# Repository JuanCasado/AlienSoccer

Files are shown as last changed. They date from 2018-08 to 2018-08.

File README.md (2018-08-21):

# AlienSoccer

This project was made by a team of three students that I was part of at Complubot.

We built two robots that played soccer coordinately with a ball that emited infrared light.
The robots were able to detect the ball as well as recognize certain parts of the field like the white limitational lines on it that the robots couldn't cross. Also they detected the field's walls as well as each other using ultrasounds.
Both robots where identically built and the operated with the same software, anyway we had different game modes like goalkeeper or player to modify their behavior.

[View in prezi (Spanish)](https://prezi.com/view/UruUJdG32kYzkdQXmuUq "prezi")

## Main caracteristics
* **High modularity:** the robots had eight processors distributed along them, each one was in charge of a specific task, making every part of the robot independent of the others. We detected wich parts where connected to the robot and operate eith them. Also one independant part could make all its functionality without the others. This made much easier the building procces because we could work in multiple parts of the robot at the same time, also testing them was faster. If one part was damaged during a game we could replace it completely with a new one in less than a minute, also the same part could operate in any robot.
* **Friendly interface:** the robots had a set of buttons, a cirular array of leds and a speaker so at any moment we could be displaying whatever the robots were seeing by their sensors. Having a nice interface was critical mainly because it made testing much easier and faster.
* **Fast processing:** We had had eight Arduino processors distributed along each robot so we where doing hadrware parallelism at any time, the robots could reach a max cycle of sensor refresing of 50ms including processing the information, and decision making.

## Parts of the robots
* **Compass:** The robots could know where they were facing to target the enemy goal.
* **Ultrasounds:** The robots could measure distances of the walls and detect objects.
* **Ball sensor:** Each robot had a "donut" of sensor arroun it, the function of this "donut" was to determine the possition and distance of the ball.
* **UI:** thanks to a set of buttons, a speaker and a circular array of leds we could "talk" to the robot.
* **Floor sensors:** We had four arrays of six sensors each that could read the wite lines of the field.
* **Motors:** Along with the ball sensors this was one of the critical parts of the robot. The robots had for motor each disposed in an X form to make an omnidirectional platform. Each motor was ruled by one proccesor wich made PID control to the motor, the four motor processors were ruled by another one wich made PID control with the facing possition and the ball position and distance to decide the target velocities of the motors, the processors comunicated by i2c.
* **Main board:** we had an arduino Mega as master of all the other seven processors, here the robots made the most critical decissions.

[Mr.BlissfulGrin](http://www.mrblissfulgrin.com "mrblissfulgrin")

[Complubot](http://complubot.com/inicio/ "complubot")

## Promotional video
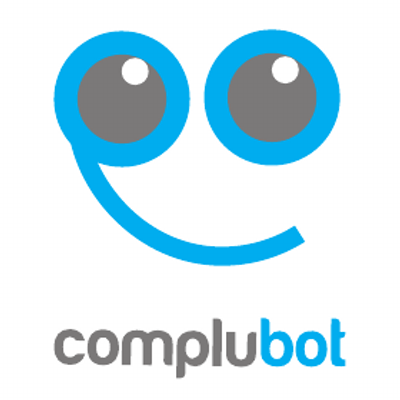
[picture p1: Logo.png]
Imperdibles2.0 Complubot
Imperdibles2.0 (http://www.youtube.com/watch?v=aCtYLtXQVko) 
**Share the video with:** [https://youtu.be/aCtYLtXQVko](https://youtu.be/aCtYLtXQVko "https://youtu.be/aCtYLtXQVko")

## Fist tests
FistTest (https://youtu.be/rDMKiselTD4)

**Share the video with:** [https://youtu.be/rDMKiselTD4](https://youtu.be/rDMKiselTD4 "https://youtu.be/rDMKiselTD4")

## Images
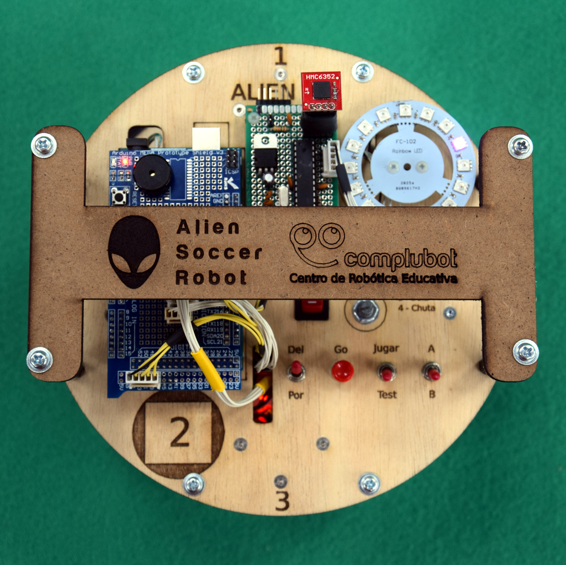
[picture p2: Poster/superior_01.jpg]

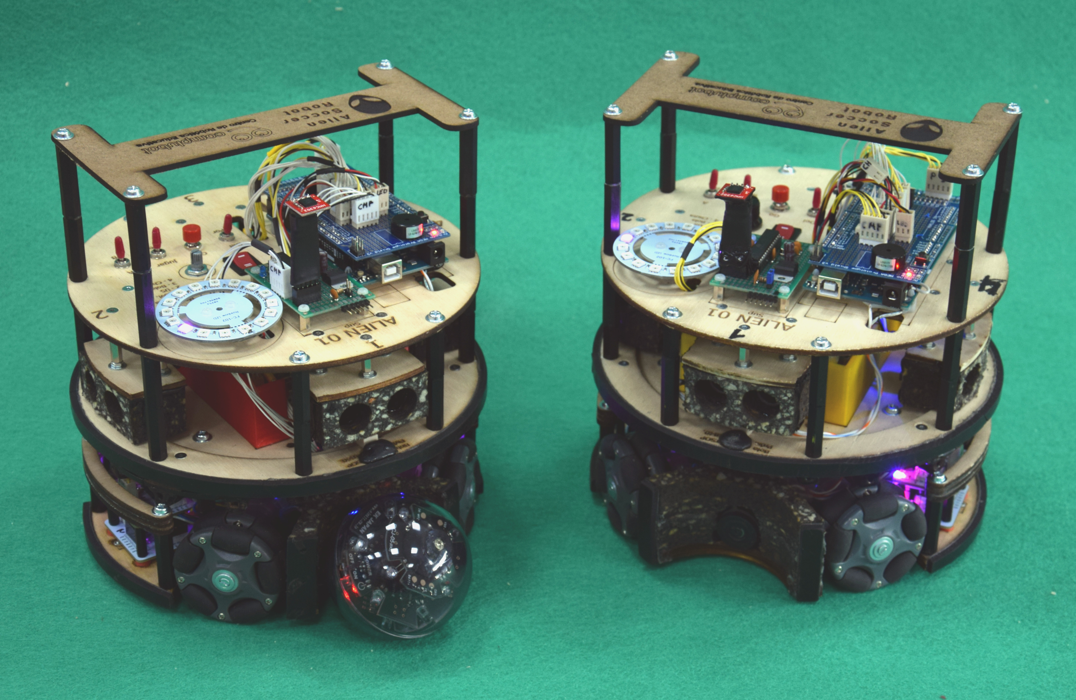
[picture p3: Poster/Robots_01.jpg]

Complubot
Complubot
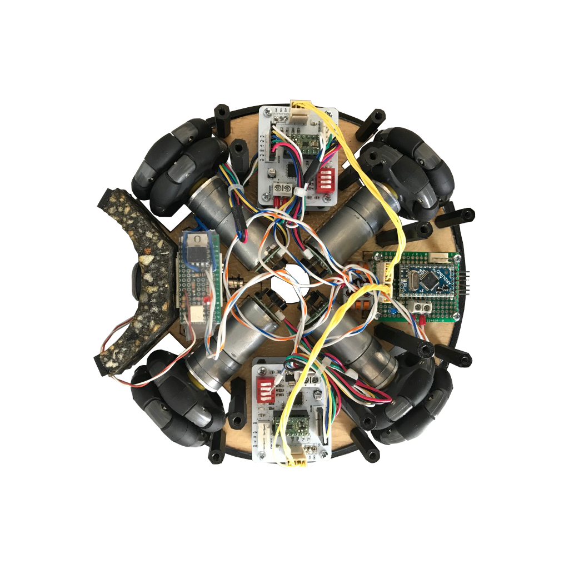
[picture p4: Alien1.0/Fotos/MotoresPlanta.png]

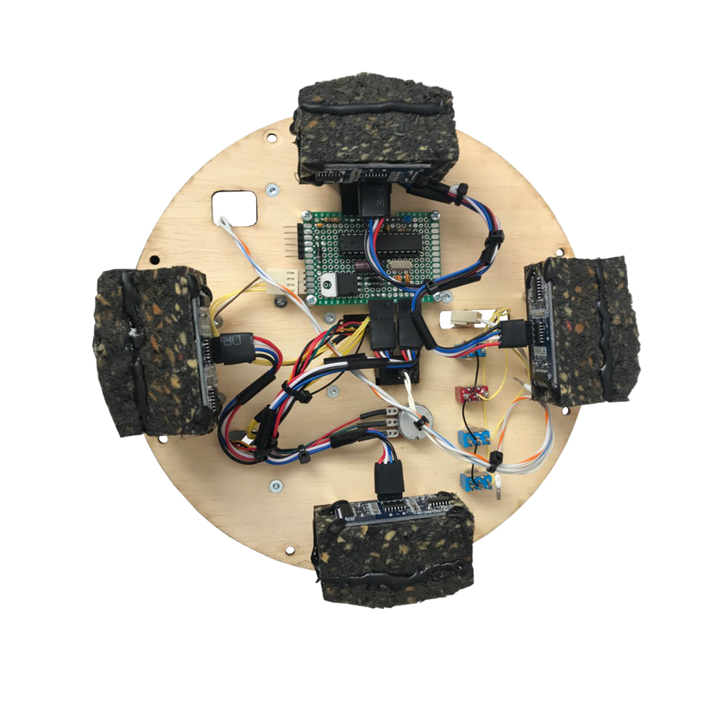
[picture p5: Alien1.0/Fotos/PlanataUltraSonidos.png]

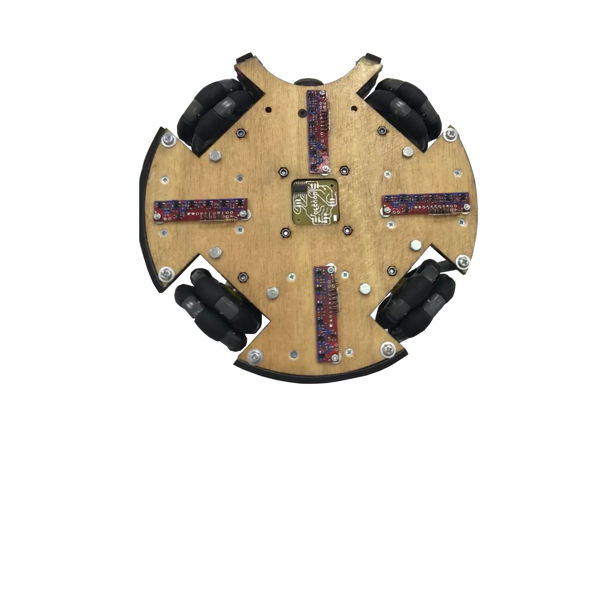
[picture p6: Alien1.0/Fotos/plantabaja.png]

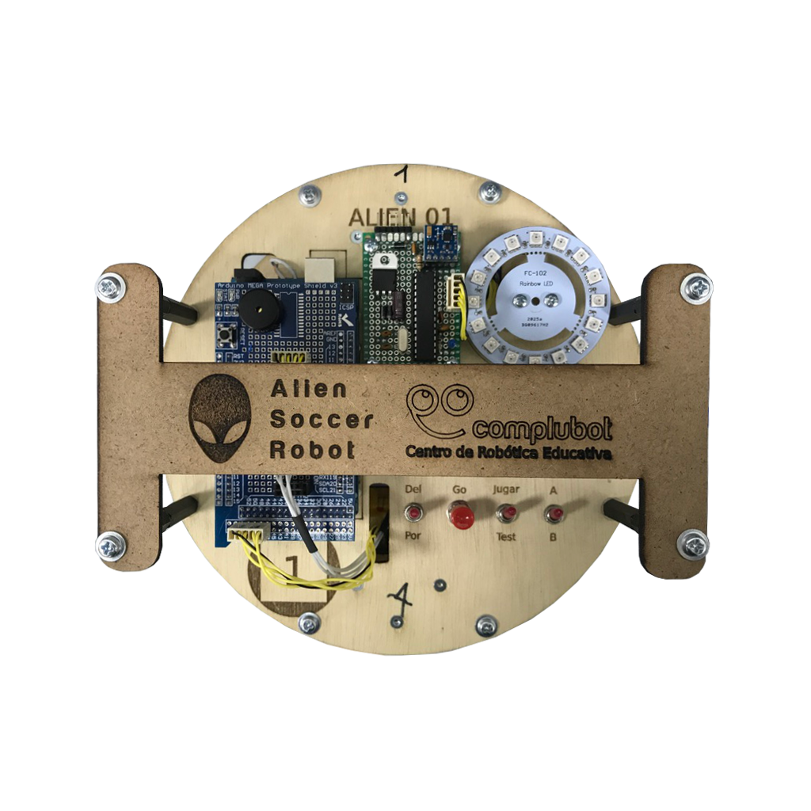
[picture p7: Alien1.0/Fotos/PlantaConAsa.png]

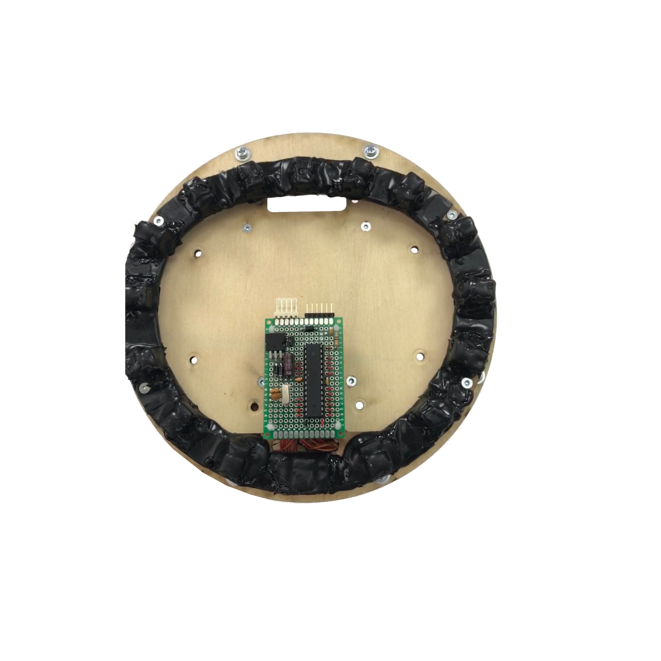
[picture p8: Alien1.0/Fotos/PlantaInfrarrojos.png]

Complubot
Complubot
Complubot
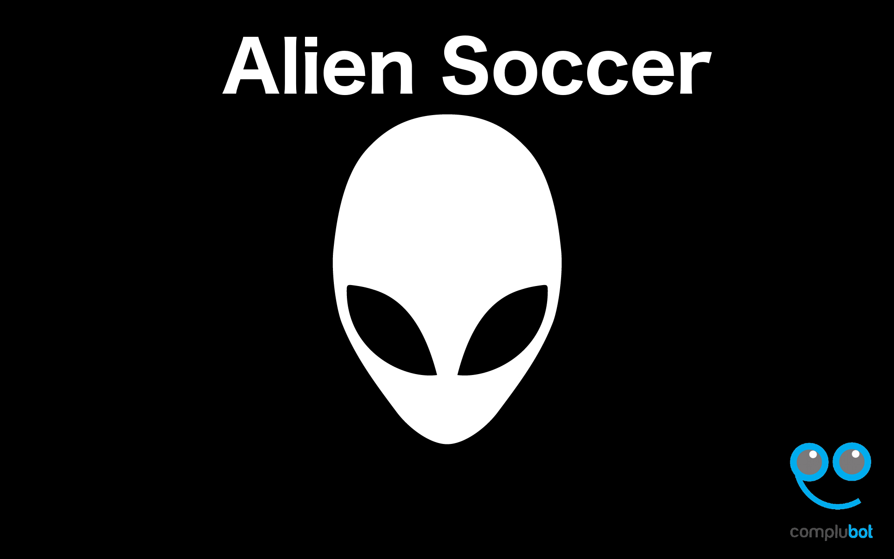
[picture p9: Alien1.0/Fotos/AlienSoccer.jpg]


Project done by Juan Casado Ballesteros

[Mr.BlissfulGrin](http://www.mrblissfulgrin.com "mrblissfulgrin")

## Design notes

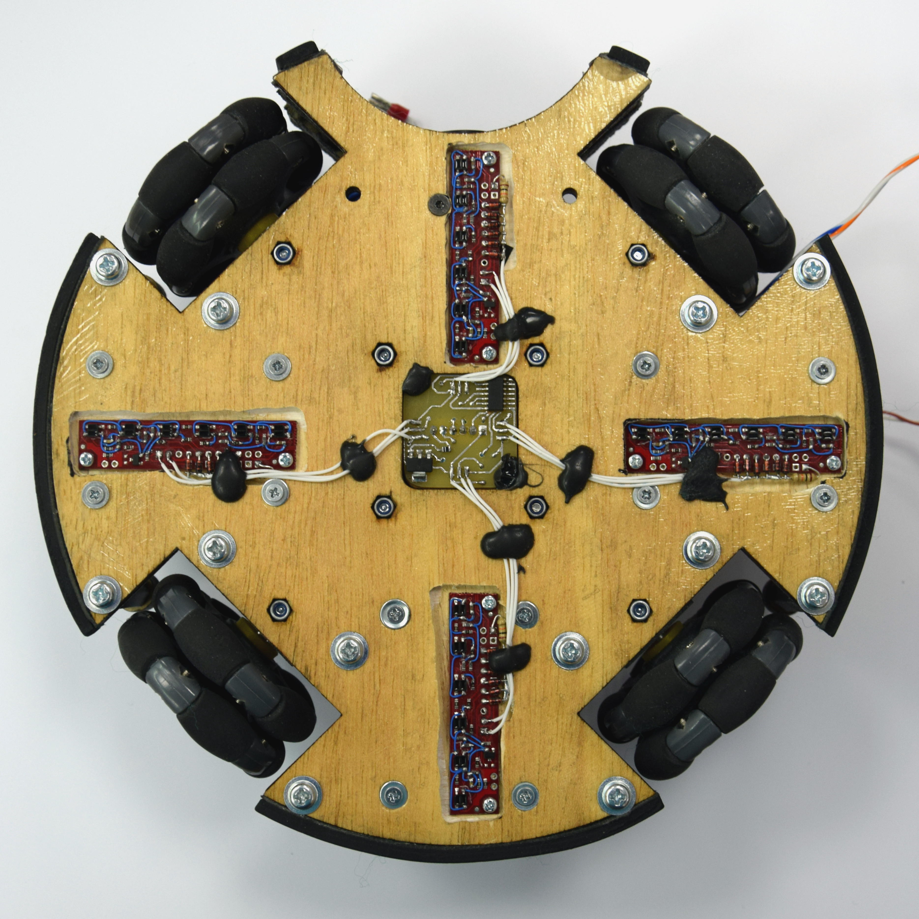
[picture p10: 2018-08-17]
Alien1.0/Poster/inferior.jpg

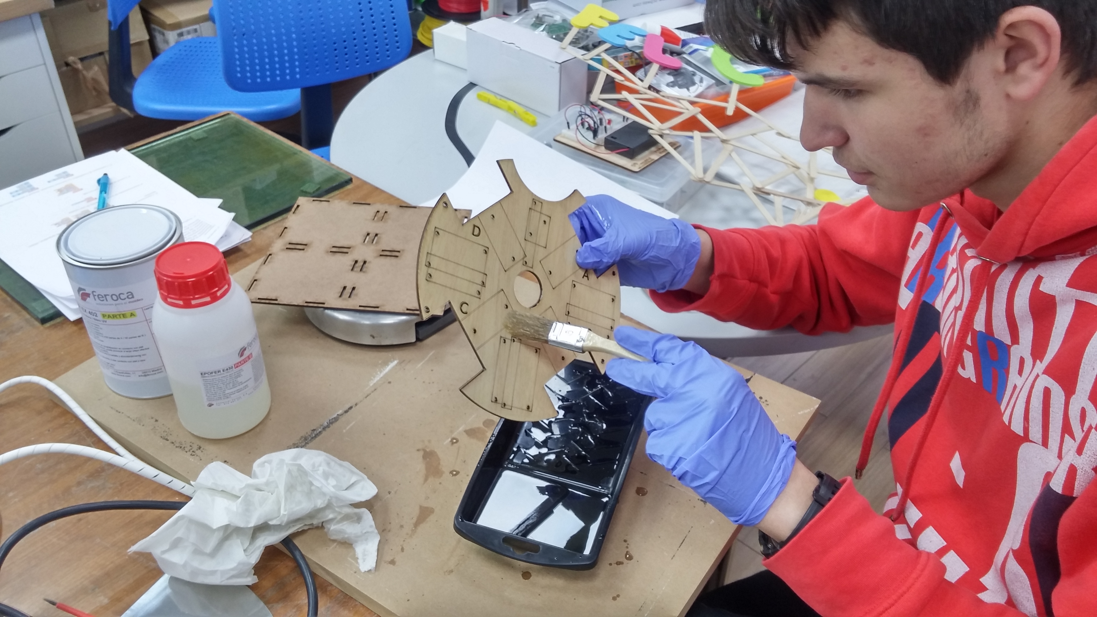
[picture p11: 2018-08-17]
Alien1.0/Poster/20170323_155203_HDR.jpg

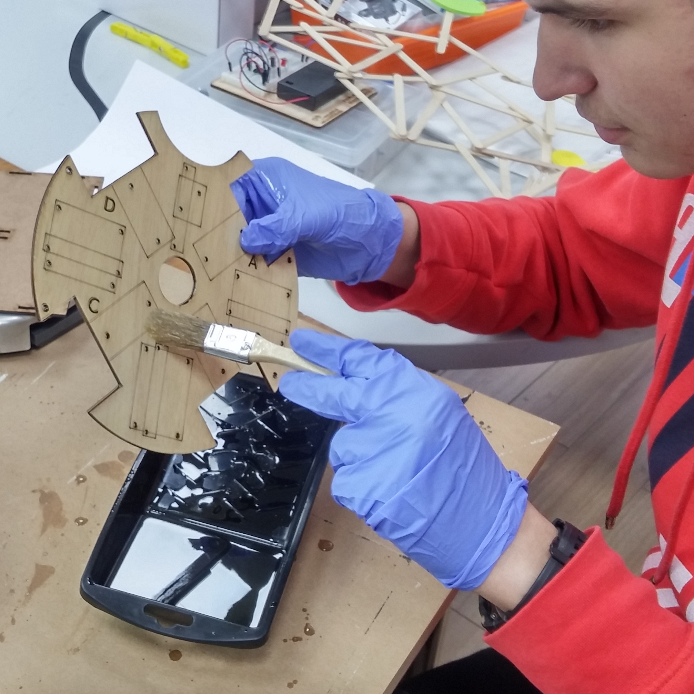
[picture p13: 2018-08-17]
Alien1.0/Poster/resina_01.jpg

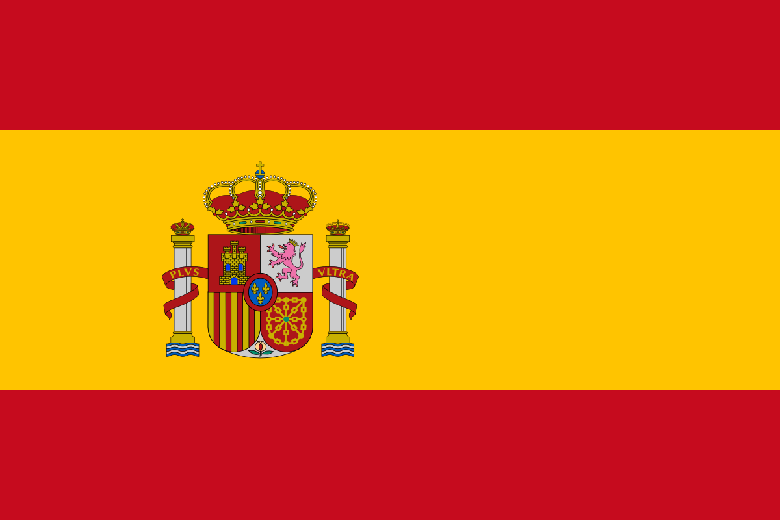
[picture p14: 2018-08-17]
Alien1.0/Poster/Flag_of_Spain.png

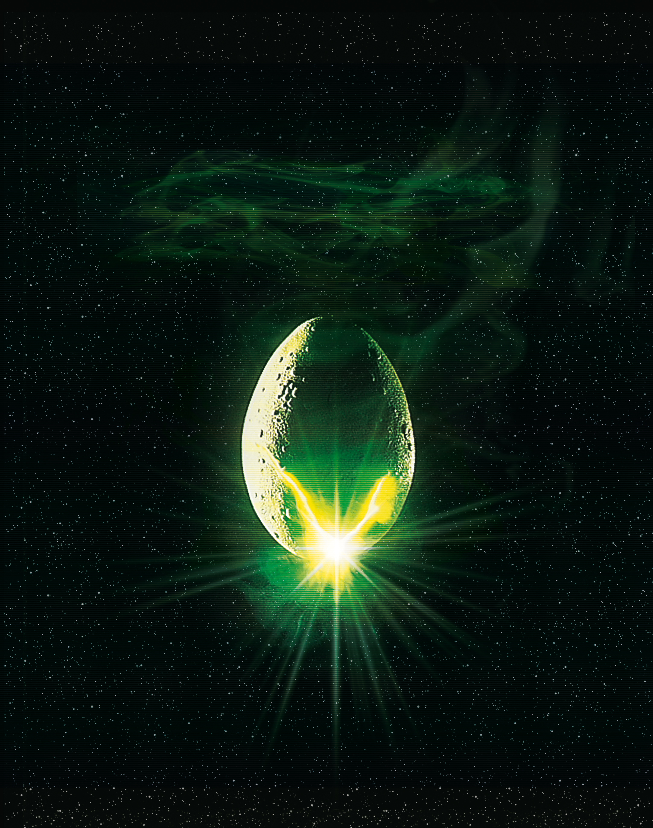
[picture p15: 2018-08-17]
Alien1.0/Poster/cc1d4e6140e174dd6c340d02d83366ad.jpeg

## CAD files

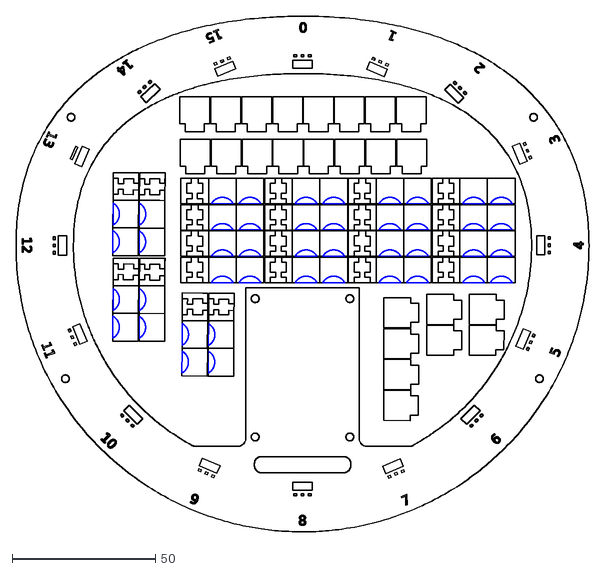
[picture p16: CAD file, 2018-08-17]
Alien1.0/Alien_Corte_Laser/Alien_ball_04.dxf
199.7 x 179.7

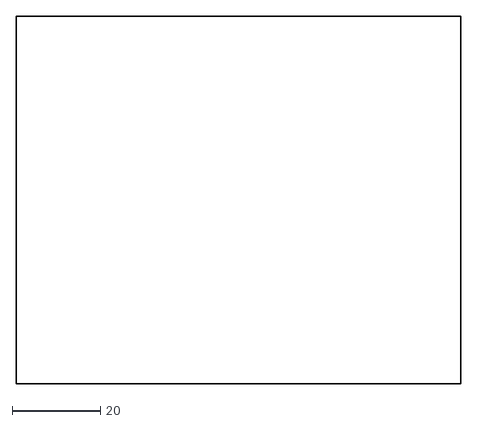
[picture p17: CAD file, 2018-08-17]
Alien1.0/KiCad/Alien_Power/pcb_shape.dxf
101.0 x 83.4

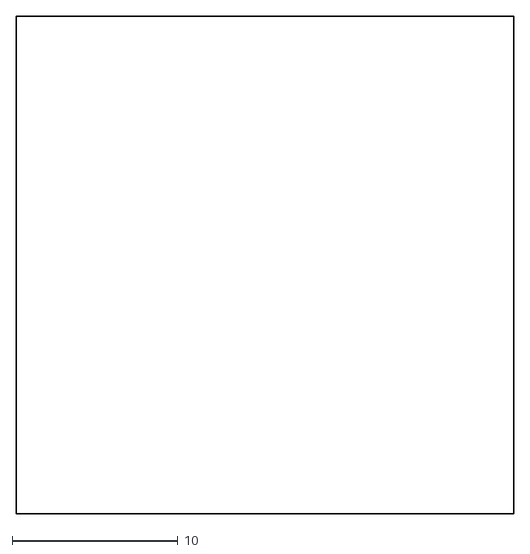
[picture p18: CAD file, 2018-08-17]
Alien1.0/KiCad/Alien_S_Suelo/pcb_shape.dxf
30.0 x 30.0

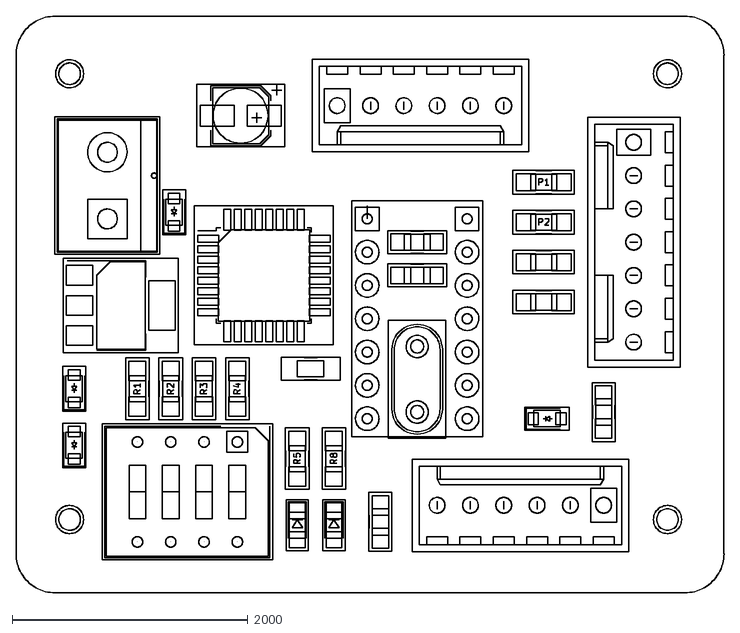
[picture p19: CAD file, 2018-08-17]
Alien1.0/KiCad/Driver_alien/Driver_alien-brd.dxf
6000.2 x 4889.2

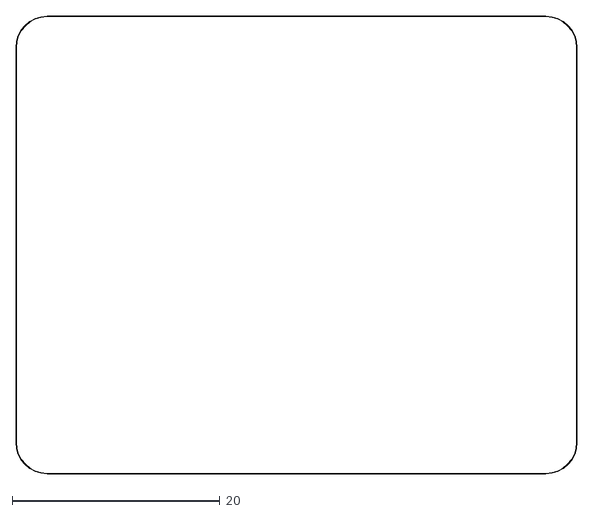
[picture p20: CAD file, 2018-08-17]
Alien1.0/KiCad/pcb_shape.dxf
54.0 x 44.0

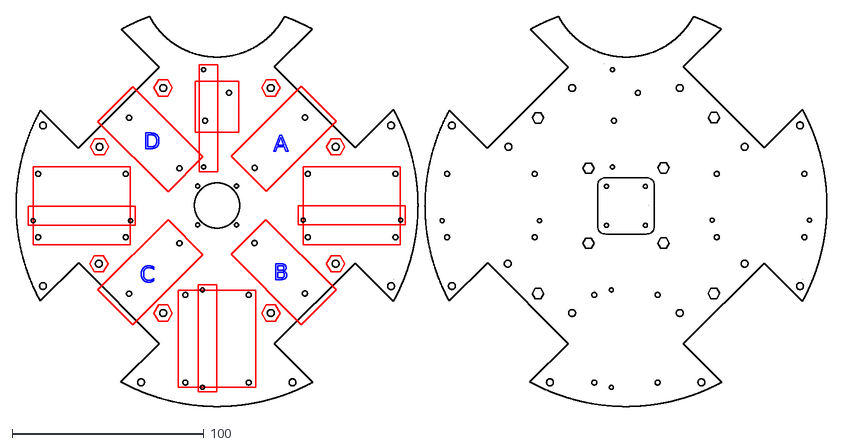
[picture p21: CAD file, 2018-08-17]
Alien1.0/Alien_Corte_Laser/Alien_motor_base_final.dxf
423.1 x 203.5

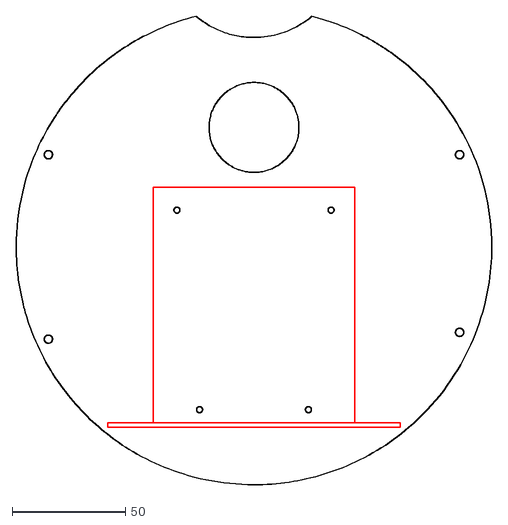
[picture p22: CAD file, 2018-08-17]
Alien1.0/Alien_Corte_Laser/Alien_Intermedio_Base_01.dxf
209.7 x 206.6

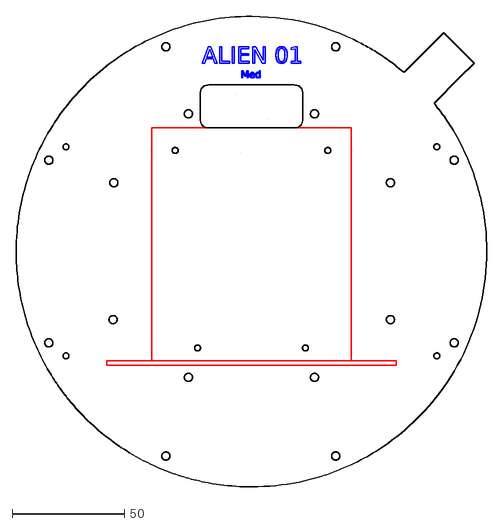
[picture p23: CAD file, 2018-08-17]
Alien1.0/Alien_Corte_Laser/Alien_Intermedio_Base_02_recorte.dxf
209.6 x 209.6

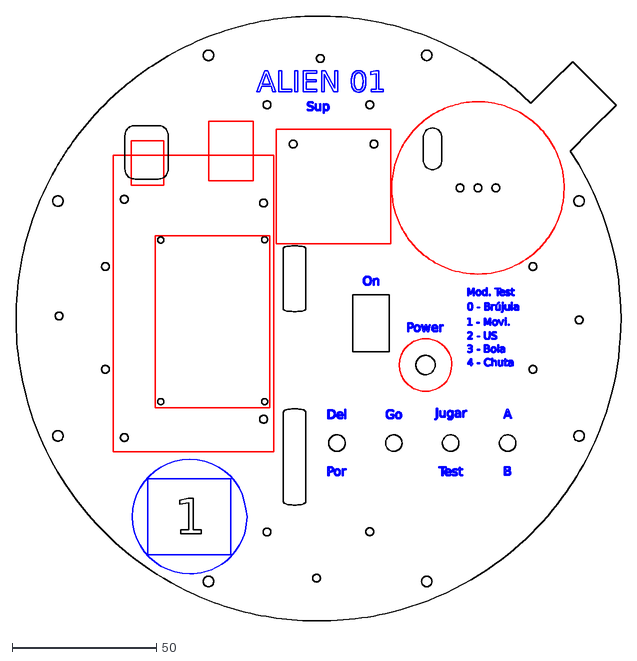
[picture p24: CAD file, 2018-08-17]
Alien1.0/Alien_Corte_Laser/Alien_Master_Base_03_recorte.dxf
209.6 x 209.6

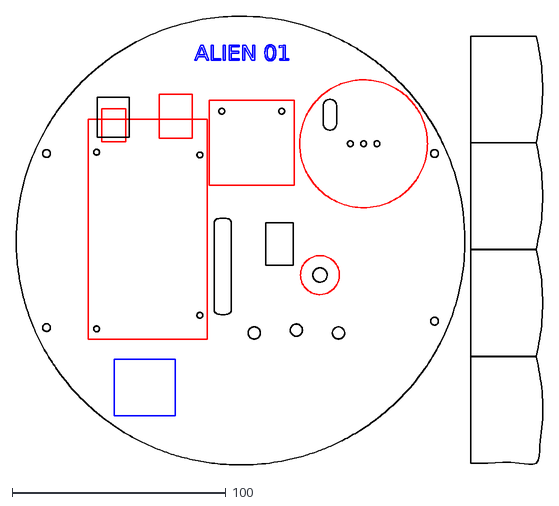
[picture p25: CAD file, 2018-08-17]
Alien1.0/Alien_Corte_Laser/Alien_Master_Base_01.dxf
246.1 x 210.1

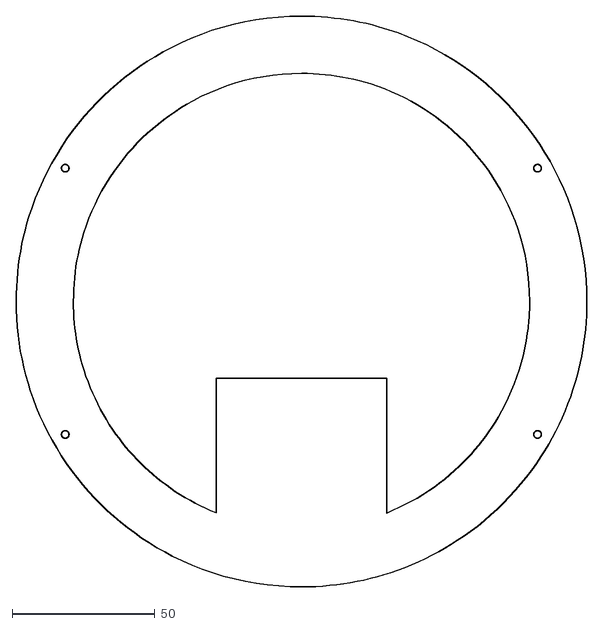
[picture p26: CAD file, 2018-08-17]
Alien1.0/Alien_Corte_Laser/Alien_ball_01.dxf
199.6 x 199.6

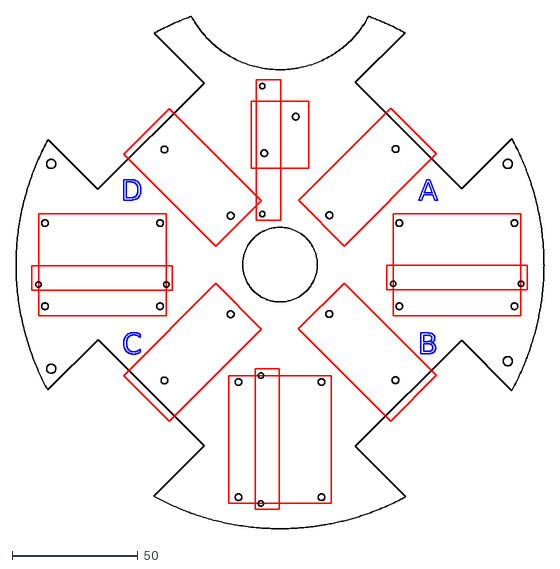
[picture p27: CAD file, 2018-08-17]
Alien1.0/Alien_Corte_Laser/Alien_motor_base_01.dxf
209.7 x 203.5

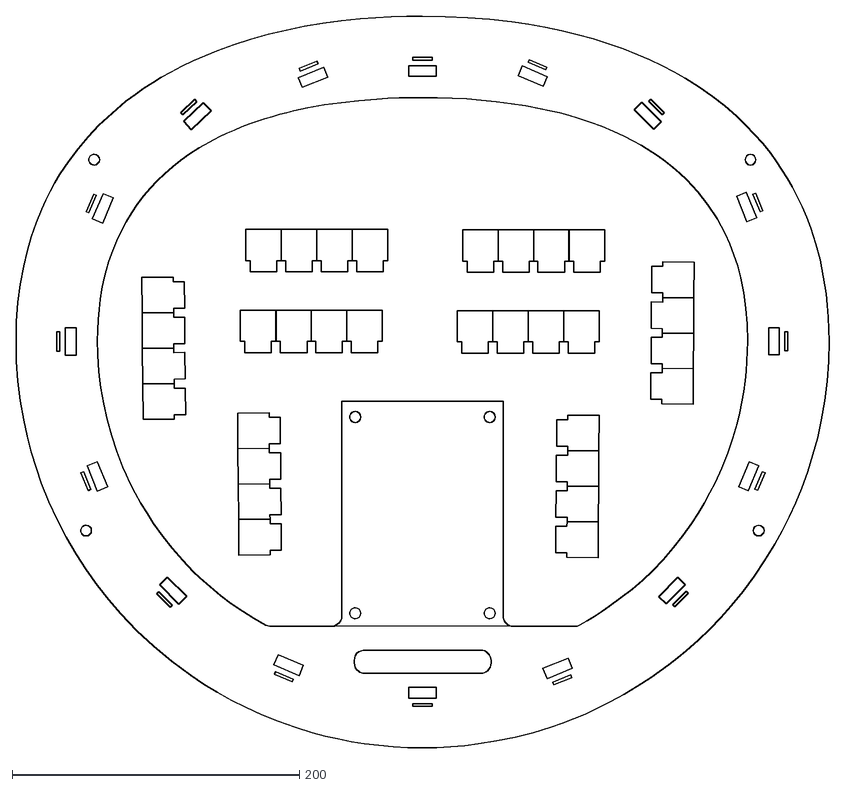
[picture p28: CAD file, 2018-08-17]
Alien1.0/Alien_Corte_Laser/Alien_ball_02.dxf
566.1 x 509.4

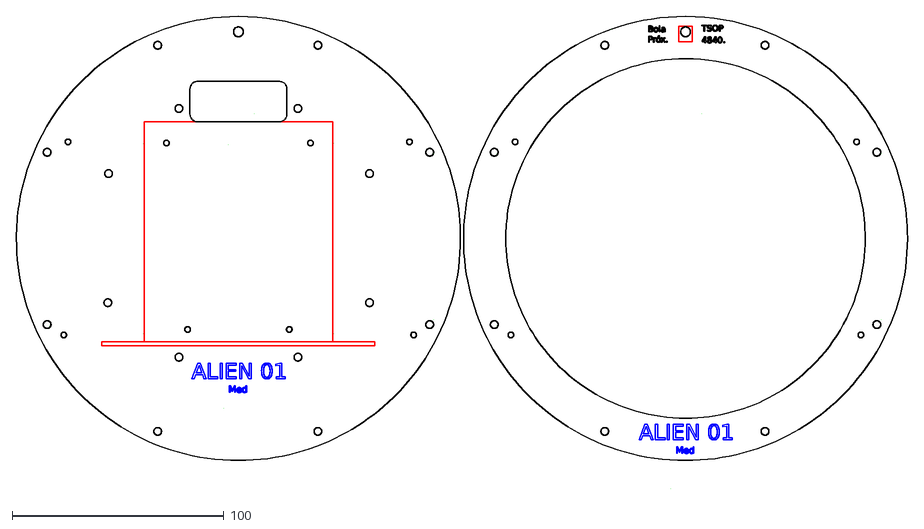
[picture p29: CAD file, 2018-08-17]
Alien1.0/Alien_Corte_Laser/Alien_Intermedio_Base_04.dxf
420.7 x 222.9

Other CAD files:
Alien1.0/Alien_Corte_Laser/Alien_Master_Base_03-2.dxf
Alien1.0/Alien_Corte_Laser/Alien_motor_base_03_contra.dxf
Alien1.0/Alien_Corte_Laser/Asa_01.dxf
Alien1.0/Alien_Corte_Laser/Alien_ball_01-2.dxf
Alien1.0/Alien_Corte_Laser/Alien_Chutador_01.dxf
Alien1.0/Alien_Corte_Laser/Alien_Intermedio_Base_02.dxf
Alien1.0/Alien_Corte_Laser/Alien_Intermedio_Base_03.dxf
Alien1.0/Alien_Corte_Laser/Alien_Master_Base_02-2.dxf
Alien1.0/Alien_Corte_Laser/Alien_Master_Base_02.dxf
Alien1.0/Alien_Corte_Laser/Alien_Master_Base_03.dxf
Alien1.0/Alien_Corte_Laser/Alien_motor_base_02.dxf
Alien1.0/Alien_Corte_Laser/Alien_motor_base_03.dxf
Alien1.0/Alien_Corte_Laser/Driver_alien-brd.dxf
Alien1.0/Alien_Corte_Laser/espumas_us_01.dxf
Alien1.0/Alien_Corte_Laser/espumas_us_02.dxf

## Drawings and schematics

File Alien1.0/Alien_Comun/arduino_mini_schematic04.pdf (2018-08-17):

# ARDUINO MINI 04

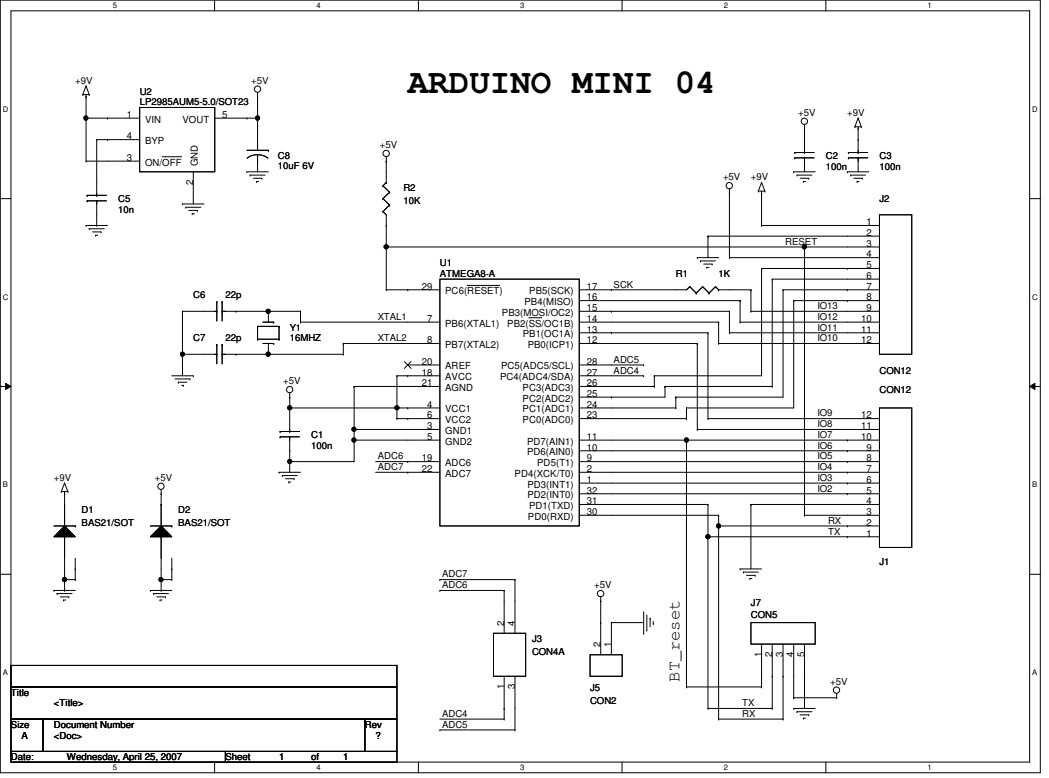
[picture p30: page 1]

PB0(ICP1) 12 PB1(OC1A) 13 PB2(SS/OC1B) 14 PB3(MOSI/OC2) 15 PB4(MISO) 16 PB5(SCK) 17

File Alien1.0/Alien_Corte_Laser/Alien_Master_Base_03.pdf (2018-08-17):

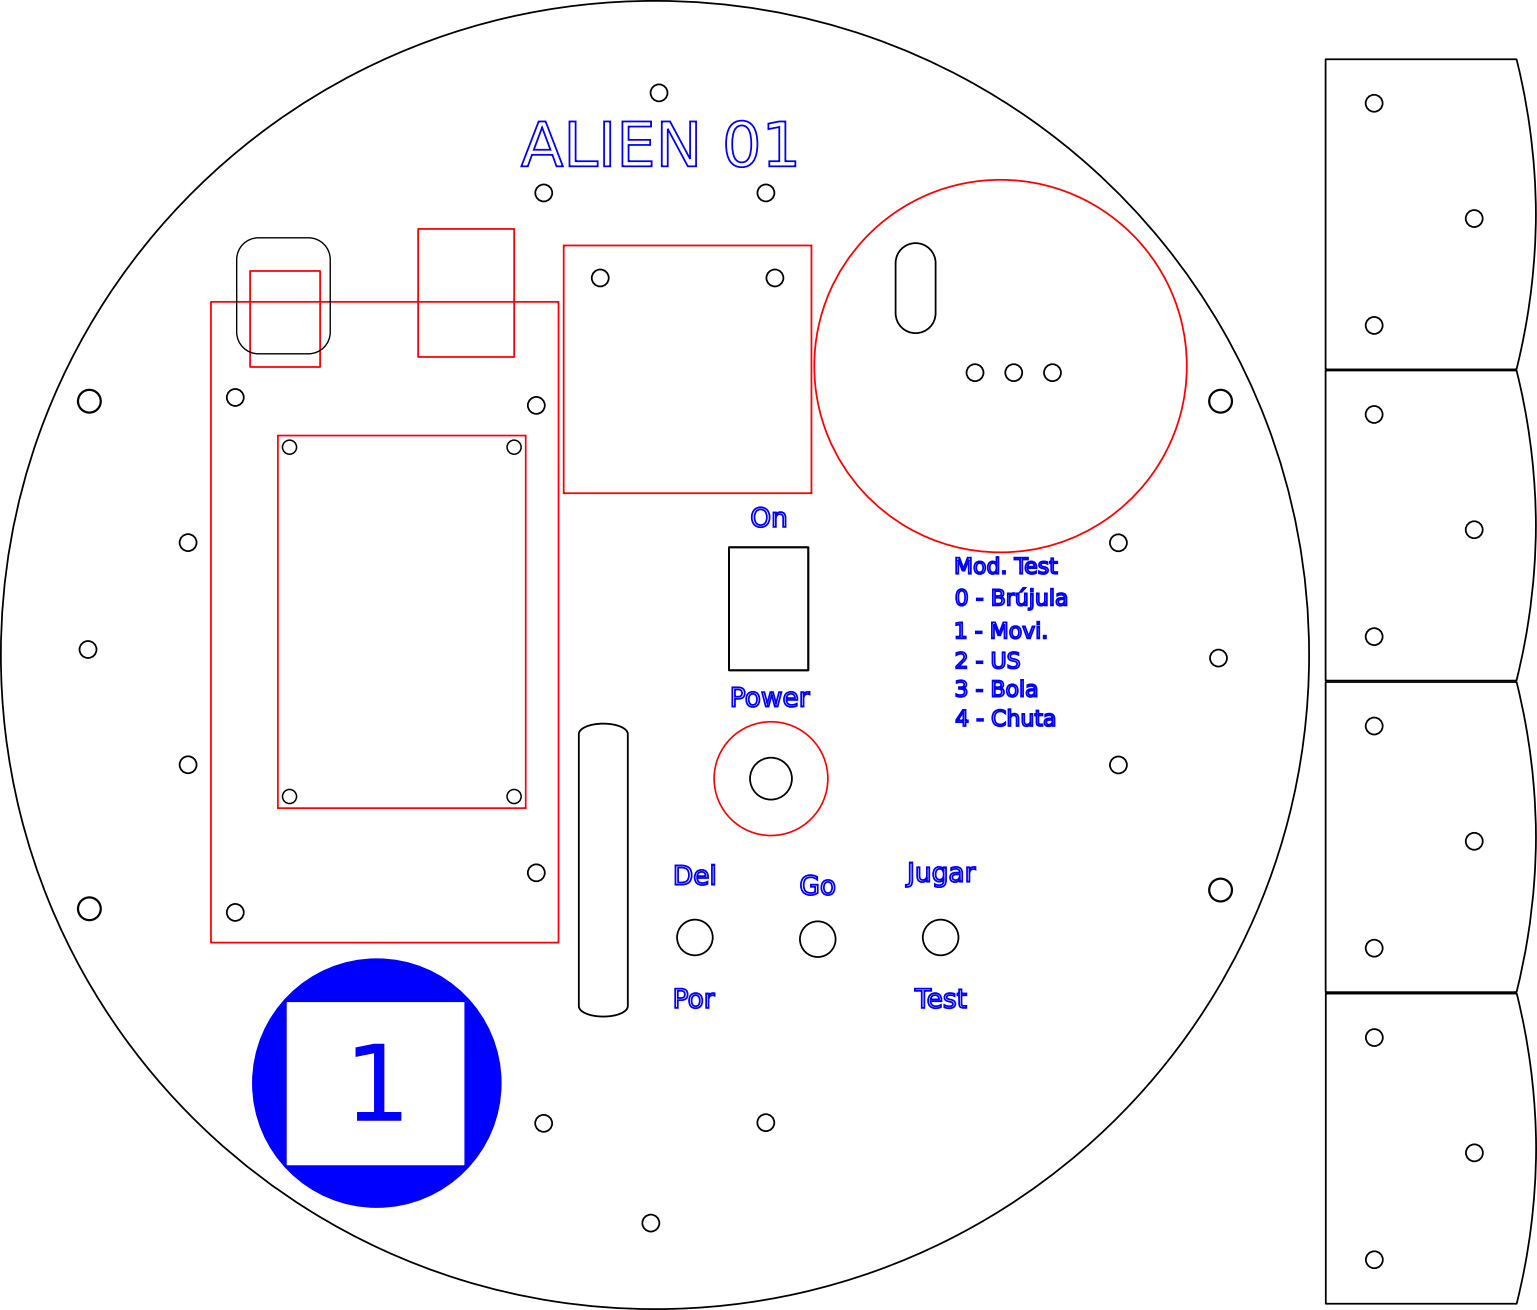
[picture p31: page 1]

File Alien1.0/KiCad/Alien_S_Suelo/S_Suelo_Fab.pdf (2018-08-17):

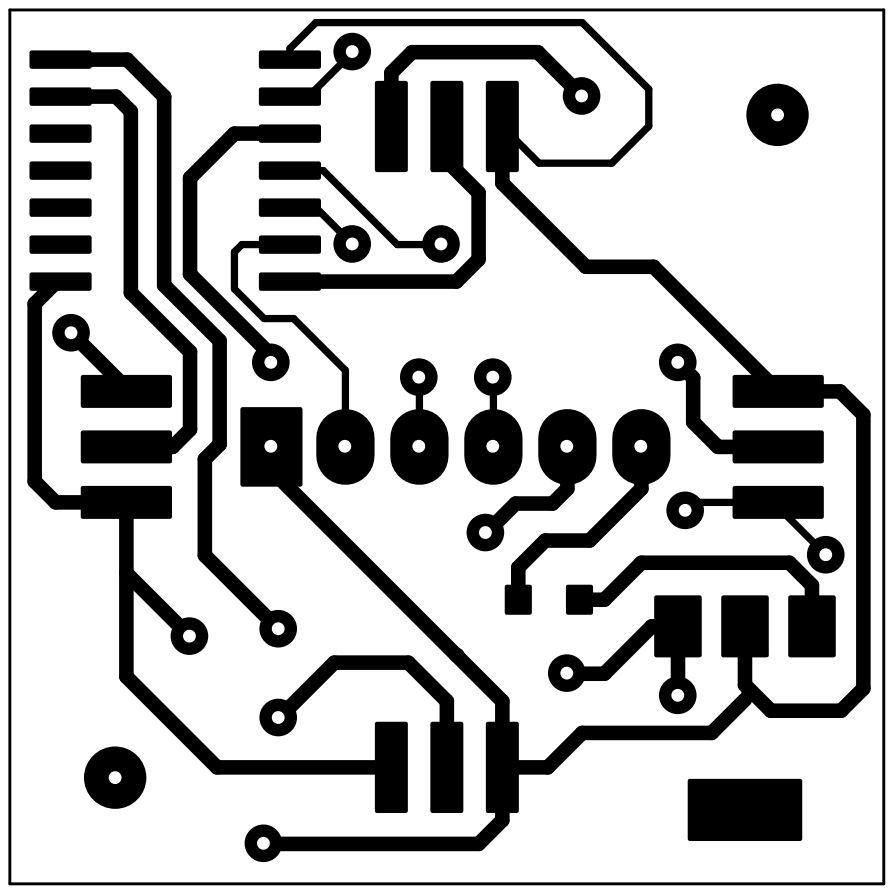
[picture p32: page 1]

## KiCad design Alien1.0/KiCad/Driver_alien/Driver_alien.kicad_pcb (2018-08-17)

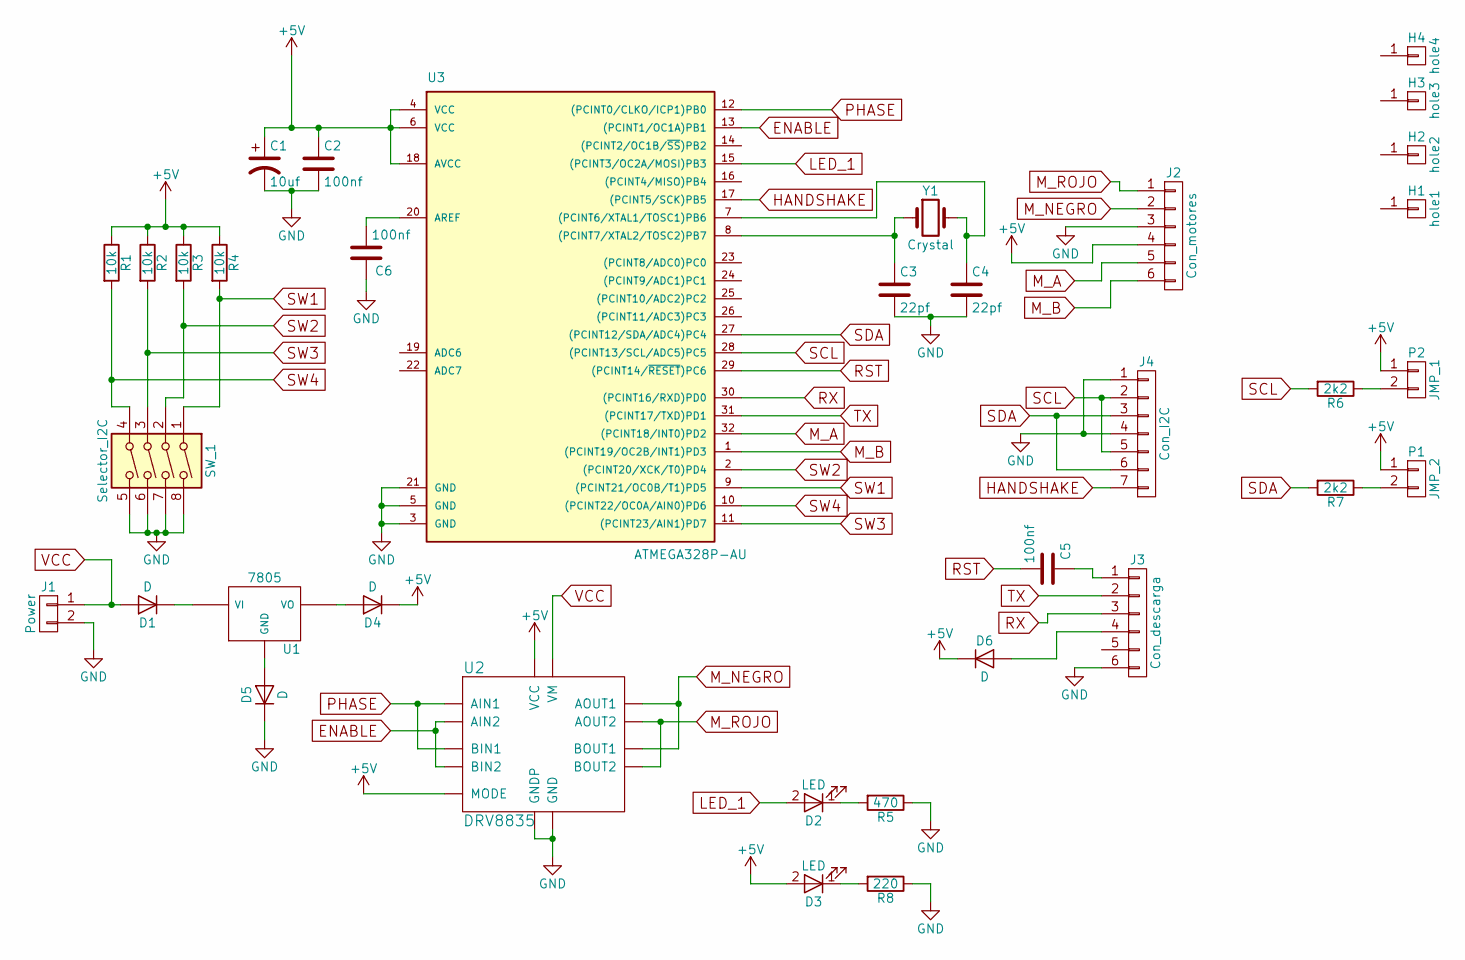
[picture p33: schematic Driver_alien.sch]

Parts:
C1: 10uf; CP_Elec_4x5.3
C2, C5, C6: 100nf; C_0805_HandSoldering
C3, C4: 22pf; C_0805_HandSoldering
D1, D4, D5, D6: D; D_0805
D2, D3: LED; LED_0805
H1: hole1; Hole3mm
H2: hole2; Hole3mm
H3: hole3; Hole3mm
H4: hole4; Hole3mm
J1: Power; bornier2
J2: Con_motores; Molex_KK-6410-06_06x2.54mm_Straight
J3: Con_descarga; Molex_KK-6410-06_06x2.54mm_Straight
J4: Con_I2C; Molex_KK-6410-07_07x2.54mm_Straight
P1: JMP_2; R_0805_HandSoldering
P2: JMP_1; R_0805_HandSoldering
R1, R2, R3, R4: 10k; R_0805_HandSoldering
R5: 470; R_0805_HandSoldering
R6, R7: 2k2; R_0805_HandSoldering
R8: 220; R_0805_HandSoldering
SW_1: Selector_I2C; SW_DIP_x4_W7.62mm_Slide
U1: 7805; SOT-223
U2: DRV8835
U3: ATMEGA328P-AU; TQFP-32_7x7mm_Pitch0.8mm
Y1: Crystal; Resonator-2pin_w8.0mm_h3.5mm

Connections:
+5V: C1.1, C2.1, D3.2 (A), D4.1 (K), D6.1 (K), J2.4, P1.1, P2.1, R1.1, R2.1, R3.1, R4.1, U2.2 (VCC), U2.7 (MODE), U3.4 (VCC), U3.6 (VCC), U3.18 (AVCC)
ENABLE: U2.3 (BIN2), U2.5 (AIN2), U3.13 ((PCINT1/OC1A)PB1)
GND: C1.2, C2.2, C3.2, C4.2, C6.1, D5.1 (K), J1.2, J2.3, J3.6, J4.1, J4.4, R5.1, R8.1, SW_1.5, SW_1.6, SW_1.7, SW_1.8, U2.1 (GND), U2.14 (GNDP), U3.3 (GND), U3.5 (GND), U3.21 (GND)
HANDSHAKE: J4.7, U3.17 ((PCINT5/SCK)PB5)
LED_1: D2.2 (A), U3.15 ((PCINT3/OC2A/MOSI)PB3)
M_A: J2.5, U3.32 ((PCINT18/INT0)PD2)
M_B: J2.6, U3.1 ((PCINT19/OC2B/INT1)PD3)
M_NEGRO: J2.2, U2.9 (AOUT1), U2.11 (BOUT1)
M_ROJO: J2.1, U2.10 (AOUT2), U2.12 (BOUT2)
unnamed: C3.1, U3.8 ((PCINT7/XTAL2/TOSC2)PB7), Y1.1
unnamed: C4.1, U3.7 ((PCINT6/XTAL1/TOSC1)PB6), Y1.2
unnamed: C5.1, J3.1
unnamed: C6.2, U3.20 (AREF)
unnamed: D1.1 (K), U1.VI
unnamed: D2.1 (K), R5.2
unnamed: D3.1 (K), R8.2
unnamed: D4.2 (A), U1.VO
unnamed: D5.2 (A), U1.GND
unnamed: D6.2 (A), J3.4
unnamed: P1.2, R7.1
unnamed: P2.2, R6.1
PHASE: U2.4 (BIN1), U2.6 (AIN1), U3.12 ((PCINT0/CLKO/ICP1)PB0)
RST: C5.2, U3.29 ((PCINT14/~RESET~)PC6)
RX: J3.3, U3.30 ((PCINT16/RXD)PD0)
SCL: J4.2, J4.5, R6.2, U3.28 ((PCINT13/SCL/ADC5)PC5)
SDA: J4.3, J4.6, R7.2, U3.27 ((PCINT12/SDA/ADC4)PC4)
SW1: R4.2, SW_1.1, U3.9 ((PCINT21/OC0B/T1)PD5)
SW2: R3.2, SW_1.2, U3.2 ((PCINT20/XCK/T0)PD4)
SW3: R2.2, SW_1.3, U3.11 ((PCINT23/AIN1)PD7)
SW4: R1.2, SW_1.4, U3.10 ((PCINT22/OC0A/AIN0)PD6)
TX: J3.2, U3.31 ((PCINT17/TXD)PD1)
VCC: D1.2 (A), J1.1, U2.13 (VM)

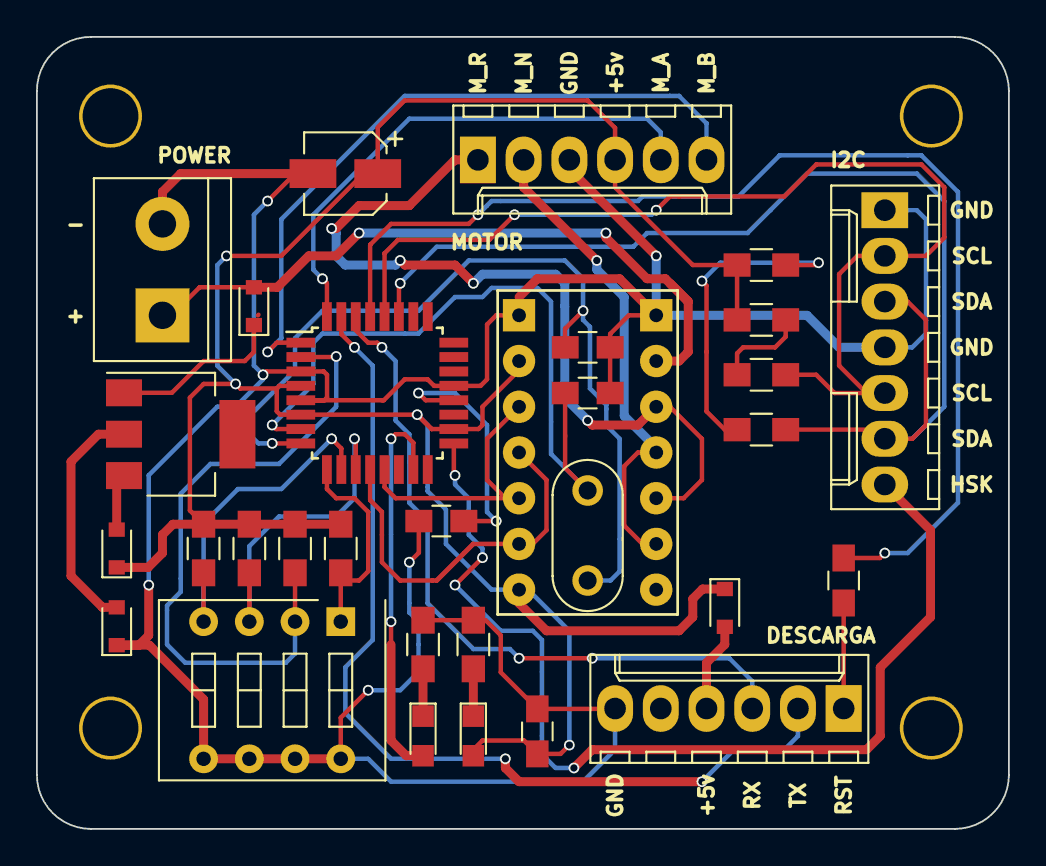
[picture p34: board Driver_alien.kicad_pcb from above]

Board: 2 copper layers, 54.0 x 44.0 mm, 35 parts (0 on the bottom side), 32 nets.

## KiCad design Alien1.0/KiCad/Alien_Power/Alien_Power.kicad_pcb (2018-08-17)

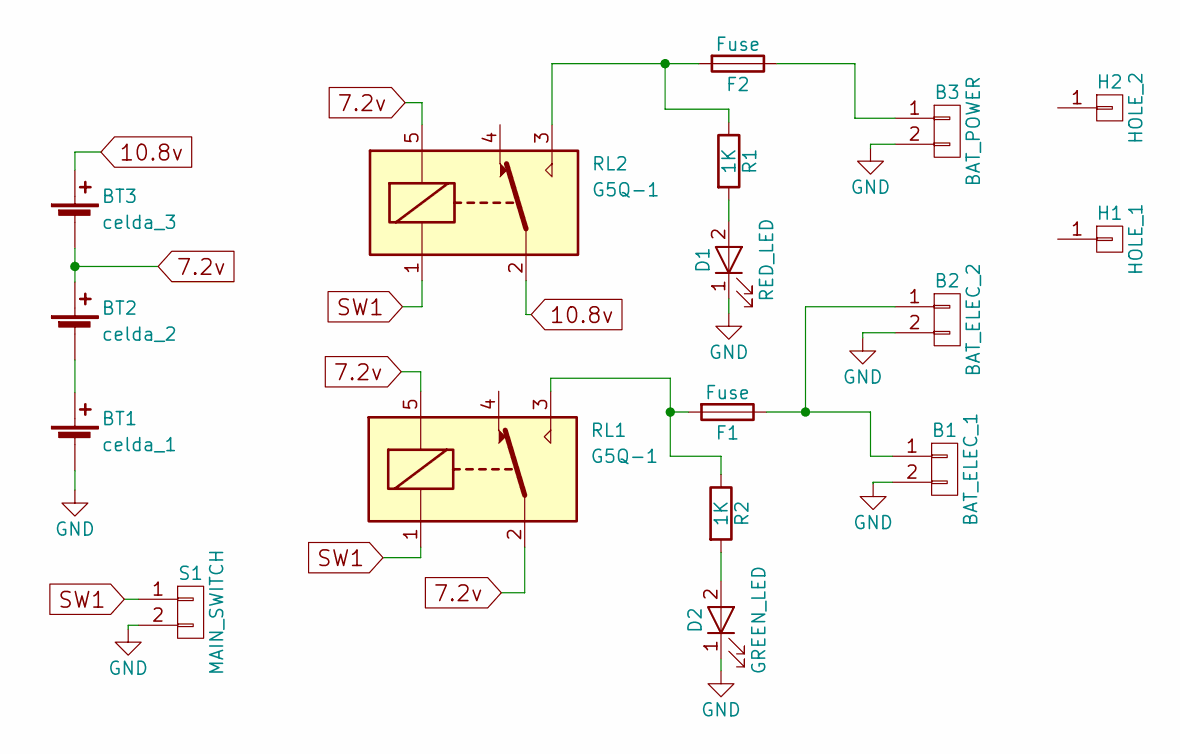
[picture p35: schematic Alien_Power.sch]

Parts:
B1: BAT_ELEC_1; bornier2
B2: BAT_ELEC_2; bornier2
B3: BAT_POWER; bornier2
BT1: celda_1; Portapila
BT2: celda_2; Portapila
BT3: celda_3; Portapila
D1: RED_LED; LED_D3.0mm
D2: GREEN_LED; LED_D3.0mm
F1, F2: Fuse
H1: HOLE_1; Hole3mm
H2: HOLE_2; Hole3mm
R1, R2: 1K; R_Axial_DIN0204_L3.6mm_D1.6mm_P7.62mm_Horizontal
RL1, RL2: G5Q-1; Relay
S1: MAIN_SWITCH; Molex_KK-6410-02_02x2.54mm_Straight

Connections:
7.2v: BT2.1 (+), BT3.2 (-), RL1.2, RL1.5, RL2.5
10.8v: BT3.1 (+), RL2.2
GND: B1.2, B2.2, B3.2, BT1.2 (-), D1.1 (K), D2.1 (K), S1.2
unnamed: B1.1, B2.1, F1.1
unnamed: B3.1, F2.1
unnamed: BT1.1 (+), BT2.2 (-)
unnamed: D1.2 (A), R1.2
unnamed: D2.2 (A), R2.2
unnamed: F1.2, R2.1, RL1.3
unnamed: F2.2, R1.1, RL2.3
SW1: RL1.1, RL2.1, S1.1

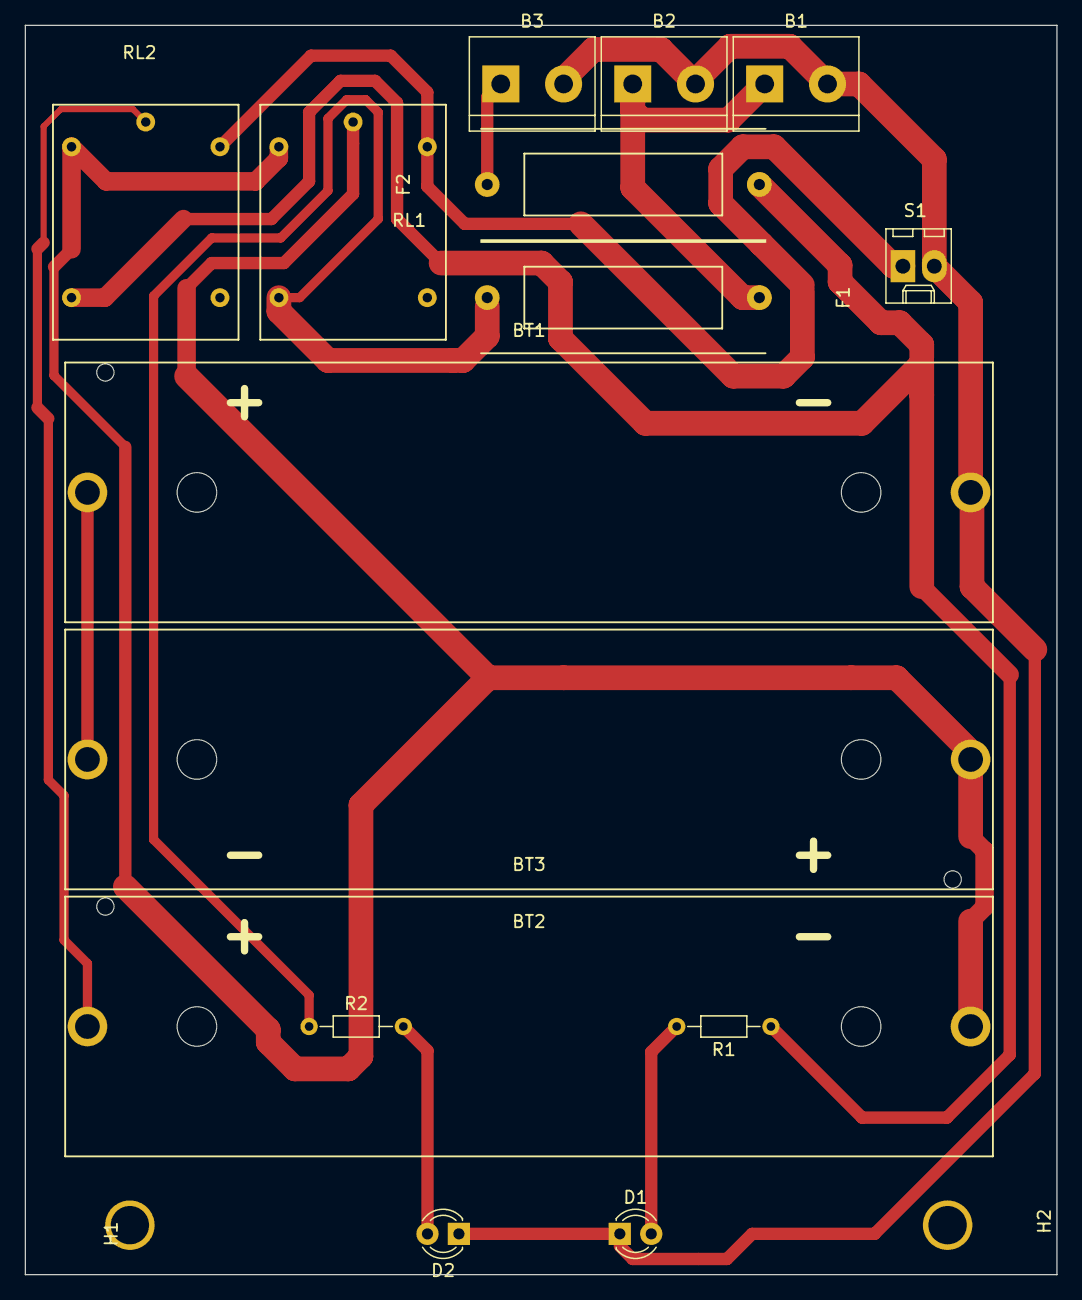
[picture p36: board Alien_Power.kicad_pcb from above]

Board: 2 copper layers, 83.4 x 101.0 mm, 17 parts (0 on the bottom side), 11 nets.

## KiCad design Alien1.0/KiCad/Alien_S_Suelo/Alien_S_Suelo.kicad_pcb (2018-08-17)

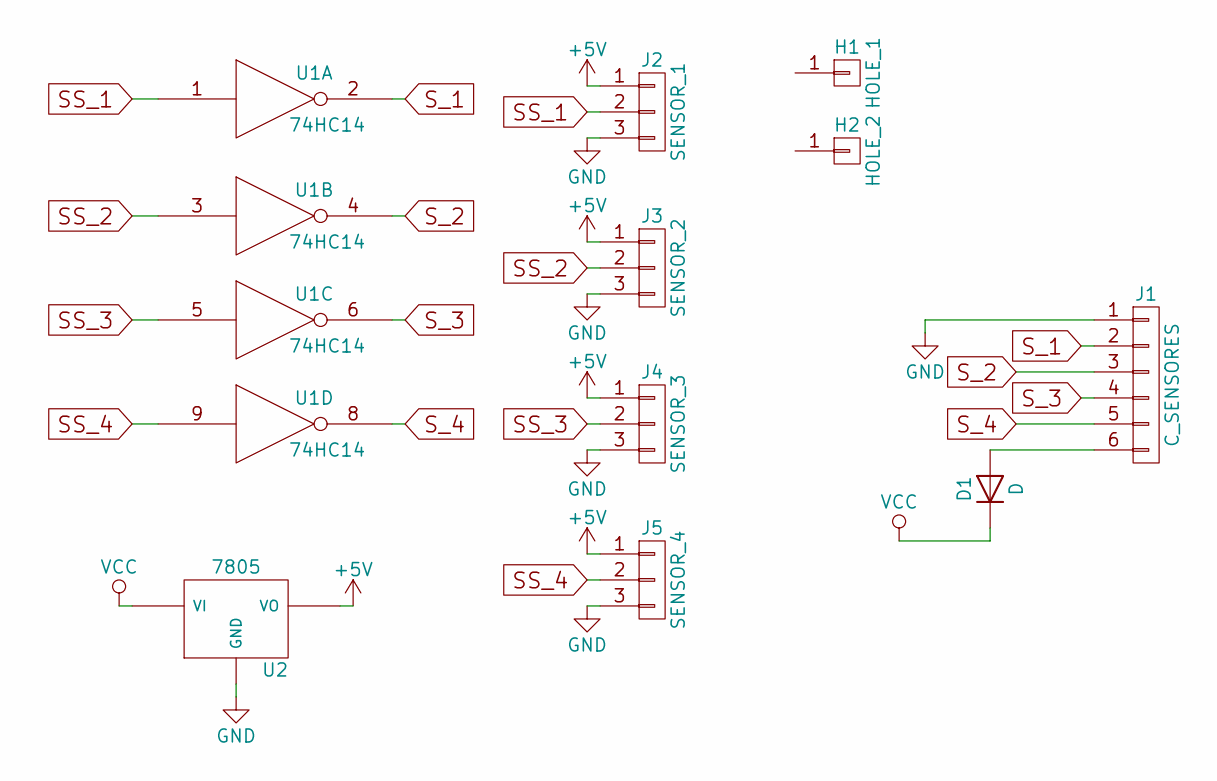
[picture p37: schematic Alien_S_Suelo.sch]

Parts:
D1: D; D_0805
H1: HOLE_1; Hole3mm
H2: HOLE_2; Hole3mm
J1: C_SENSORES; Molex_KK-6410-06_06x2.54mm_Straight
J2: SENSOR_1; Con_soldado_3
J3: SENSOR_2; Con_soldado_3
J4: SENSOR_3; Con_soldado_3
J5: SENSOR_4; Con_soldado_3
U1: 74HC14; SO-14
U2: 7805; SOT-223

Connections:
+5V: J2.1, J3.1, J4.1, J5.1, U1.+5V, U2.VO
GND: J1.1, J2.3, J3.3, J4.3, J5.3, U1.GND, U2.GND
unnamed: D1.2 (A), J1.6
SS_1: J2.2, U1.1
SS_2: J3.2, U1.3
SS_3: J4.2, U1.5
SS_4: J5.2, U1.9
S_1: J1.2, U1.2
S_2: J1.3, U1.4
S_3: J1.4, U1.6
S_4: J1.5, U1.8
VCC: D1.1 (K), U2.VI

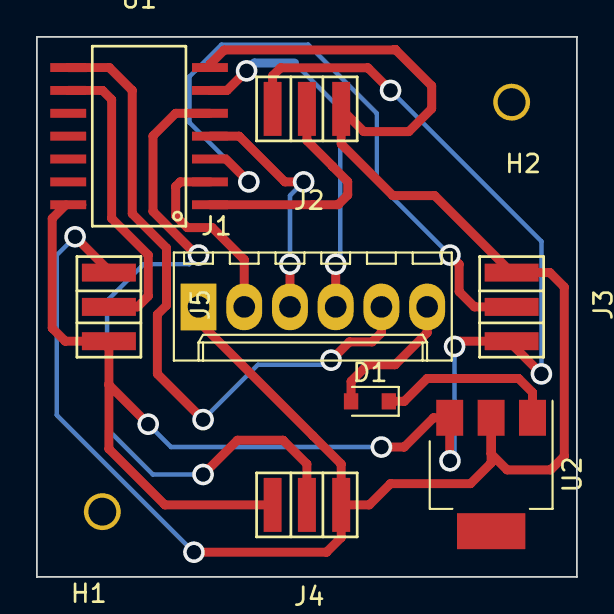
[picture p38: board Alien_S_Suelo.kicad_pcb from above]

Board: 2 copper layers, 30.0 x 30.0 mm, 10 parts (0 on the bottom side), 12 nets.

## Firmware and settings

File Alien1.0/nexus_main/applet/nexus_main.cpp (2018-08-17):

#include "WProgram.h"
#include "nexus.h"
#include "oled_160.h"
#include "brujula.h"
#include <Wire.h>
#include <MsTimer2.h>

#define TRES_US 0
#define CUATRO_US 1

//definimos el tipo de brujula que usamos
//#define CMPS03
//#define HMC5362

//Posiciones X e Y para trazar un c\u00edrculo con 48 LEDs
//Se usan para indicar los movimientos y los sensores
//Las cordenadas indican el centro del circulo
  
#include "WProgram.h"
void periodica(void);
void setup();
void loop();
void comunica_xbee(void);
void actualiza_motores(void);
void actualiza_sensores(void);
void actualiza_lecturas_ardusonic(void);
void actualiza_lecturas_arduball(void);
void actualiza_sensores_suelo(void);
void actualiza_consumo_roller(void);
byte espera_serie(byte p_serie,byte n_datos);
void pruebas(void);
void juega_delantero(void);
void centra_delantero(void);
void manda_xbee(void);
void jugar (void);
void mueve_robot(byte movimiento);
void gira_robot(char giro_robot);
void pivota(char pivotar);
void vel_robot(byte vel);
void vel_max_robot(byte vel);
void para_robot(void);
void chuta(void);
void voy_detras_de_la_bola(void);
void tira_porteria(void);
void activa_roller(byte control_roller);
void centra_tiro(void);
void corrige_mov_us(void);
void despejar(void);
void prueba_arduball(void);
void visualiza_pot_arduball(byte reset);
void visualiza_grafica_barras_arduball(byte reset);
void visualiza_grafica_circular_arduball(byte reset);
void prueba_ardumotion(void);
void seleciona_movimiento_ardumotion(byte reset);
void prueba_ardusonic(void);
void monitor_baterias(void);
void prueba_brujula(void);
byte centra_brujula (int parar);
void prueba_chutador(void);
void prueba_roller(void);
void sigue_pelota(void);
void juega_portero(void);
void centra_portero(void);
void portero_preventivo(void);
void portero_despeja(void);
void centra_portero_ir(void);
void recibe_xbee(void);
int c48_x[48]={
   43, 43, 42, 40, 37, 34, 30, 26, 22, 16, 11, 6,0,-6,-11,-16,-22,-26,-30,-34,-37,-40,-42,-43,
  -43,-43,-42,-40,-37,-34,-30,-26,-22,-16,-11,-6,0, 6, 11, 16, 22, 26, 30, 34, 37, 40, 42, 43};
int c48_y[48]={
  0, 6, 11, 16, 22, 26, 30, 34, 37, 40, 42, 43, 43, 43, 42, 40, 37, 34, 30, 26, 22, 16, 11, 6,
  0,-6,-11,-16,-22,-26,-30,-34,-37,-40,-42,-43,-43,-43,-42,-40,-37,-34,-30,-26,-22,-16,-11,-6,};  

//Variable comun donde guardamos lo que recibimos por el puerto serie
byte respuesta=0, rellena_medidas=0;

int respuesta_int=0;

int consumo_roller=0;
int conta=0;
byte maquina_centrado_b=0, estoy_centrado=0;
char centradito_porteria=0;

byte marca_gol_amarillo=0, si_xbee=0, rol_robot=0;

//Variable modificada por varias funciones que se usa para controlar el movimiento del robot
int direccion=255, direccion_anterior=0;

//Variables del selector
byte selector=0;
byte selector_anterior=255;

//Variable para la identificacion del robot
byte robot;

//Variables para el movimiento
int velocidad_robot=-1;
int velocidad=10;
int movimiento=255;
int movimiento_anterior=0;
int velocidad_anterior=0;
int giro_robot=0, giro_robot_anterior=0;
int conta_tengo_roller=0;

//Variables de arduball
byte sensor_chutador = 0;
byte sensor_maximo=49, ultimo_sensor_maximo;
byte distancia_bola, ultima_distancia_bola;
byte sensores[24];

//Variables de la brujula
int posicion_robot_actual=0;
int brujula_inicial;
long espera_brujula_chutador=0;


//Variables de ardusonic
int us_izquierdo=0, us_derecho=0, us_trasero=0, us_frontal=0;
int us_c_izquierdo=0, us_c_derecho=0, corrige_us_d=0, corrige_us_i=0;

//Varibles de el XBee
int xbee=false;
char del_pelota=false;

//Flags para la actualizacion de sensores
byte flag_brujula = false, flag_us = false, flag_ir = false, flag_motores = false, flag_roller = false;

byte posicion_x=0, posicion_y=0;


//Sensores
struct SENSORES{
  int suelo_id,suelo_dd,suelo_dt,suelo_it, medida_dd, medida_id, medida_dt, medida_it;
  int us_izq,us_der,us_tra,us_fron;
  int brujula;
  int b_pot,b_ele;
};
SENSORES sensor;

byte n_us = TRES_US;

void periodica(void)
{
#define VECES_BRUJULA 4
#define VECES_US 2
#define VECES_IR 2
#define VECES_ROLLER 4 
#define VECES_MOTORES 4 

  static byte flag_conta_brujula = VECES_BRUJULA;
  static byte flag_conta_us = VECES_US;
  static byte flag_conta_ir = VECES_IR;
  static byte flag_conta_roller = VECES_ROLLER;
  static byte flag_conta_motores = VECES_MOTORES;

  //Actualiza brujula
  flag_conta_brujula--;
  if (flag_conta_brujula == 0);
  {
    flag_brujula = true;
    flag_conta_brujula = VECES_BRUJULA;
  }

  //Actualiza ultrasonidos
  flag_conta_us--;
  if (flag_conta_us == 0);
  {
    flag_us = true;
    flag_conta_us = VECES_US;
  }

  //Actualiza los ir's
  flag_conta_ir--;
  if (flag_conta_ir == 0);
  {
    flag_ir = true;
    flag_conta_ir = VECES_IR;
  }

  //Actualizamos sensores suelo
  actualiza_sensores_suelo();

  //Actualiza consumo roller
  flag_conta_roller--;
  if (flag_conta_roller == 0);
  {
    flag_roller = true;
    flag_conta_roller = VECES_ROLLER;
  }

  //Actualiza motores
  flag_conta_motores--;
  if (flag_conta_motores == 0);
  {
    flag_motores = true;
    flag_conta_motores = VECES_MOTORES;
  }
}

void setup()
{
  //Resetea los perifericos
  resetea_perifericos();

  //Inicializa el display
  oled_ini();
  oled_opaco_transparente(OPACO);
  oled_pluma(SOLIDO);

  configura_selector();

  //Inicializa el puerto serie de Ardumotion
  Serial.begin(250000);

  //Inicializa el puerto serie de Arduball y Ardusonic
  Serial1.begin(250000);
  
  //Inicializa puerto serie XBee
  Serial3.begin(38400);
  
  //Inicializa la brujula y toma la posicion inicial 
  inicializa_brujula();
  delay(10);
  brujula_inicial = lee_brujula();

  //Configura periodica
  MsTimer2::set(10, periodica); // se ejecuta cada 10ms
  MsTimer2::start();

  //Configuramos el chutador
  digitalWrite(CHUTADOR,HIGH);
  pinMode(CHUTADOR,OUTPUT);


  //Hace un parpadeo con los 4 LED's de se\u00f1alizacion y pita dos veces el zumbador
  comprueba_led(1);
  doble_beep();
  comprueba_led(0);

  //comprobamos tipo de robot
  pinMode(TIPO_ROBOT_A, INPUT);
  pinMode(TIPO_ROBOT_B, INPUT);
  robot=(digitalRead(TIPO_ROBOT_A)+digitalRead(TIPO_ROBOT_B));

  //Muestra la pnatalla de presentacion
  pantalla_presentacion();
}

void loop() 
{
  //Interruptor en modo JUGAR
  if(digitalRead(INT_MODO) == 1)
  {
    jugar();
  }
  MsTimer2::stop();
  //Interrutor en modo AJUSTAR
  //Men\u00fa de m\u00f3dulos de prueba
  visualiza_menu();  
  while(digitalRead(GO) == 1)
  {
    selector = lee_selector();
    if(selector != selector_anterior)
    {
      if (selector_anterior != 255)
      {
        oled_caracter(selector_anterior+0x30,0,selector_anterior+2,MEDIANO,BLANCO);
        oled_texto("->",1,selector_anterior+2,MEDIANO,BLANCO);
      }
      oled_caracter(selector+0x30,0,selector+2,MEDIANO,AZUL_CLARO);
      oled_texto("->",1,selector+2,MEDIANO,AZUL_CLARO);
      oled_visualiza_entero(selector,42,117,MEDIANO);
      oled_texto_sin_formato("Selector:",0,117,MEDIANO,BLANCO);
      selector_anterior=selector;
      delay(50);
    }
  }

  //Se ha seleccionado alguno de los modulos de prueba, y entra
  espera_go();
  oled_borra_pantalla();

  switch (selector)
  {
  case 0:      //muestra el nivel de baterias
    monitor_baterias();
    break;

  case 1:      //lee el valor de los 24 sensores
    prueba_arduball();
    break;  

  case 2:     //muestra el valor del pot de ajustar la velocidad
    prueba_ardumotion();
    break;

  case 3:
    prueba_ardusonic();
    break;

  case 4:
    prueba_brujula();
    break;

  case 5:
    prueba_chutador();
    break;

  case 6:
    sigue_pelota();
    break;

  case 7:
    //Calibracion de la brujula HMC5362
    pruebas();
    break;

  case 8:
    //prueba_cmucam3();
    comunica_xbee();
    break;

  case 9:
    prueba_roller();
    break;

  default:
    break;  
  } 

  //Permite volver a mostrar el mismo elemento del menu
  selector_anterior=255;
}

void comunica_xbee(void);

int mv=0;

void comunica_xbee(void)
{
  //Borra terminal VT100
  Serial3.print(0x1B,BYTE);
  Serial3.print("[2J");
  
  if(robot == ROBOT_NEXUS_9_2)
    Serial3.println("Nexus 9.2 - Command Mode");

  else
    Serial3.println("Nexus 9.1 - Command Mode");

  Serial3.print("> ");

  while(true)
  {    
    if(Serial3.available() > 0)
    {
      switch(Serial3.read())
      {
      case 'B':
        Serial3.println();
        Serial3.print("> ");
        Serial3.print("Bat Electro: ");
        Serial3.print((promedia_ai(BAT_ELECTRO,16) * 59.0)/2500.0);
        Serial3.print("V");
        Serial3.print(" Bat Pot: ");
        Serial3.print((promedia_ai(BAT_POT,16) * 59.0)/2500.0);
        Serial3.println("V");
        Serial3.print("> ");
        break;

      case 'c':
        Serial3.println();
        Serial3.print("> ");
        Serial3.print("Posicion Brujula: ");
        Serial3.print(varia_posicion_brujula(brujula_inicial));
        Serial3.println();
        Serial3.print("> ");
        break;  

      case 'C':
        chuta();
        Serial3.println();
        Serial3.print("> ");
        break;


      case 'h':
      case 'H':
        Serial3.println();
        Serial3.println();
        Serial3.println("Ayuda");
        Serial3.println("-----");
        Serial3.println();
        Serial3.println("B   -> Tension Baterias");
        Serial3.println("c   -> Brujula");
        Serial3.println("C   -> Chuta");
        Serial3.println("I   -> Identificacion");
        Serial3.println("M   -> Mueve Robot");
        Serial3.println("P,p -> Para Robot");
        Serial3.println("S   -> Sensores Bola");
        Serial3.println("U   -> Sensores Ultrasonidos");
        Serial3.println("V   -> Ajusta Velocidad");
        Serial3.println();
        Serial3.print("> ");
        break;

      case 'I':
        beep();
        if(robot == ROBOT_NEXUS_9_2)
          Serial3.println(" Nexus 9.2");

        else
          Serial3.println(" Nexus 9.1");
        Serial3.print("> ");
        break;

      case 'M':
        while(Serial3.available() < 2);
        mv=((Serial3.read()-0x30)*10)+(Serial3.read()-0x30);
        if((mv>=0) && (mv<48))
        {
          mueve_robot(mv);
        }
        else
        {
          Serial3.println("Error");
        }
        Serial3.println();
        Serial3.print("> ");
        break;

      case 'p':
      case 'P':
        para_robot();
        Serial3.println();
        Serial3.print("> ");
        break;

      case 'S':
        actualiza_lecturas_arduball();

        Serial3.println();
        Serial3.print("> ");
        Serial3.print("Sensor Max: ");
        Serial3.print(sensor_maximo);
        Serial3.print("Distancia: ");
        Serial3.println(distancia_bola);
        Serial3.print("> ");
        break;

      case 'U':
        actualiza_lecturas_ardusonic();

        Serial3.println();
        Serial3.print("> ");
        Serial3.print("US Derecho: ");
        Serial3.print(us_derecho);
        Serial3.print(" US Izquierdo: ");
        Serial3.print(us_izquierdo);
        Serial3.print(" US Trasero: ");
        Serial3.println(us_trasero);
        Serial3.print("> ");
        break;

      case 'V':
        while(Serial3.available() < 3);
        mv=((Serial3.read()-0x30)*100)+((Serial3.read()-0x30)*10)+(Serial3.read()-0x30);
        if((mv>=0) && (mv<101))
        {
          vel_max_robot(mv);
        }
        else
        {
          Serial3.println("Error");
        }
        Serial3.println();
        Serial3.print("> ");
        break;

      default:
        Serial3.println(" what?");
        Serial3.print("> ");
        break;
      }
    }
  }
}


void actualiza_motores(void);

void actualiza_motores(void)
{
  if(flag_motores)
  {
    flag_motores = false;
    //if(direccion != direccion_anterior)
    //{
      digitalWrite(LED_4,HIGH);
      direccion_anterior=direccion;
      MsTimer2::stop();
      mueve_robot(direccion);
      MsTimer2::start();
      digitalWrite(LED_4,LOW);
    //}
  
    if(velocidad_robot != velocidad_anterior)
    {
      velocidad_anterior=velocidad_robot;
      MsTimer2::stop();
      vel_robot(velocidad_robot);
      MsTimer2::start();
    }
    
    if(giro_robot != giro_robot_anterior)
    {
      giro_robot_anterior=giro_robot;
      MsTimer2::stop();
      gira_robot(giro_robot);
      MsTimer2::start();
    }
  }
}
////////////////////////////////////////
// Archivo: actualiza_sensores
//
////////////////////////////////////////
char lee_datos_b=0;


//Funciones de los distintos sensores
void actualiza_sensores(void);
void actualiza_lecturas_ardusonic(void);
void actualiza_lecturas_arduball(void);
void actualiza_sensores_suelo(void);
void actualiza_consumo_roller(void);
byte espera_bus(byte p_serie,byte n_datos);

////////////////////////////////////////
//Funciones para actualizar los sensores
////////////////////////////////////////
//
//Esta funcion llama a los distintos sensores que han de ser actualizados.
//Estos se ejecutan con una determinada frecuencia independiente para cada uno de ellos.
void actualiza_sensores(void)
{   
  if(flag_ir)
  {
    flag_ir=false;
    MsTimer2::stop();
    actualiza_lecturas_arduball();
    MsTimer2::start();
  }
  
  if(flag_us)
  {
    flag_us=false;
    MsTimer2::stop();
    actualiza_lecturas_ardusonic();
    MsTimer2::start();
  }
    
  if (flag_brujula)
  {
    flag_brujula=false;
    MsTimer2::stop();
    posicion_robot_actual = varia_posicion_brujula(brujula_inicial);
    MsTimer2::start();
  }
  
  if(flag_roller)
  {
    flag_roller=false;
    MsTimer2::stop();
    actualiza_consumo_roller();
    MsTimer2::start();
  }
}
void actualiza_lecturas_ardusonic(void)
{
  static byte primera_vez_ardusonic = 0;
  static byte dato_us=0;

  if (primera_vez_ardusonic == 0)
  {
    if(n_us)
    {
      while(Serial1.available() > 0)
        lee_datos_b=Serial1.read();
      
      //Activamos las medidas por ultrasonidos en el ArduSonic
      Serial1.print('C');
      if(espera_serie(1,1))
      {
        dato_us = Serial1.read();
        primera_vez_ardusonic = 1;
      }
    } 
    else
    {
      while(Serial1.available() > 0)
        lee_datos_b=Serial1.read();
      
      Serial1.print('Q');
      if(espera_serie(1,1))
      {
        dato_us = Serial1.read();
        primera_vez_ardusonic = 1;
      }
    }
  }

  //Este comando solicita las medidas de todos los sensores de ultrasonidos, los recibe y los guarda
  if(n_us)
  {
    while(Serial1.available() > 0)
      lee_datos_b=Serial1.read();
    
    Serial1.print('A');
    if(espera_serie(1,4))
    {
      dato_us = Serial1.read();
      us_derecho = dato_us;
      dato_us = Serial1.read();
      us_trasero = dato_us;
      dato_us = Serial1.read();
      us_izquierdo = dato_us;
      dato_us = Serial1.read();
      us_frontal = dato_us;
    }
  }
  else
  {
    while(Serial1.available() > 0)
      lee_datos_b=Serial1.read();
    
    Serial1.print('A');
    if(espera_serie(1,3))
    {
      dato_us = Serial1.read();
      if(dato_us != 0)
        us_derecho = dato_us;

      dato_us = Serial1.read();
      if(dato_us != 0)
        us_trasero = dato_us;
      
      dato_us = Serial1.read();
      if(dato_us != 0)
        us_izquierdo = dato_us;
    }
  }
}

void actualiza_lecturas_arduball(void)
{
  #define ACUMULA_SENSOR_CHUTADOR 4
  #define N_PROMEDIOS_DB 3
  static int promedia_d_bola[N_PROMEDIOS_DB]= {0, 0, 0};
  static int conta_promedios_db=0;
  int promediado_de_b=0, db=0;
  //Los sensores de proximidad de bola se leen tantas veces como indica la constante
  //ACUMULA_SENSOR_CHUTADOR. La variable sensor_chutador se activa si aparece un nivel alto
  //en alguna de las medidas acumuladas

  static byte x=0, medidas[ACUMULA_SENSOR_CHUTADOR],primera_vez=1;
  byte contador, acumula;

  //Inicializa el buffer circular
  if(primera_vez)
  {
    for (contador =0; contador<ACUMULA_SENSOR_CHUTADOR; contador++)
      medidas[contador]=0;
    primera_vez=0;
  }
  
  while(Serial1.available() > 0)
    lee_datos_b=Serial1.read();
  
  Serial1.print('d');
  if(espera_serie(1,3))
  {
    sensor_maximo = Serial1.read();
    distancia_bola = Serial1.read();
    
    /*promedia_d_bola[conta_promedios_db]= Serial1.read();
    
    conta_promedios_db++;
    
    if(conta_promedios_db >= N_PROMEDIOS_DB)
      conta_promedios_db=0;
    
    promediado_de_b=0;
    for(db=0; db<N_PROMEDIOS_DB; db++)
      promediado_de_b= promediado_de_b + promedia_d_bola[db];
    
    distancia_bola =(promediado_de_b/N_PROMEDIOS_DB);*/

    //Siempre lee la medida de estos sensores de cerca pero los va metiendo en un buffer circular
    //Para que se tome como "bola no vista" tiene que no-verla varias veces (las del buffer) pero para "vista" solo una
    medidas[x]=Serial1.read();
  
    x++;
    if (x >= ACUMULA_SENSOR_CHUTADOR)
      x = 0;

    acumula = 0;
    for (contador =0; contador<ACUMULA_SENSOR_CHUTADOR; contador++)
      acumula = acumula +medidas[contador];

    if (acumula == 0)
      sensor_chutador = false;
    else
      sensor_chutador = true;
   
    if((sensor_maximo > 47) && (sensor_maximo < 255))
      sensor_maximo=255;
   
  }    
}

void actualiza_sensores_suelo(void)
{
  sensor.medida_dd = analogRead(SUELO_DERECHO_DEL);
  sensor.medida_id = analogRead(SUELO_IZQUIERDO_DEL);
  sensor.medida_dt = analogRead(SUELO_DERECHO_TRA);
  sensor.medida_it = analogRead(SUELO_IZQUIERDO_TRA);
    
  if((sensor.medida_dd>UMBRAL_SUELO_BLANCO) && (sensor.suelo_dd == 0))
    sensor.suelo_dd=1;
      
  if((sensor.medida_id>UMBRAL_SUELO_BLANCO) && (sensor.suelo_id == 0))
    sensor.suelo_id=1;
      
  if((sensor.medida_dt>UMBRAL_SUELO_BLANCO) && (sensor.suelo_dt == 0))
    sensor.suelo_dt=1;
      
  if((sensor.medida_it>UMBRAL_SUELO_BLANCO) && (sensor.suelo_it == 0))
    sensor.suelo_it=1;
}

void actualiza_consumo_roller(void)
{
  #define PROMEDIOS 8

  static int conta=0, acumula=0;
                
  if(conta<PROMEDIOS)
  {
    conta++;
    acumula += analogRead(CONSUMO_ROLLER);
  }
  else
  {
    acumula=acumula>>3;
    consumo_roller= acumula;
    acumula=0;
    conta=0;
  }
}

byte espera_serie(byte p_serie,byte n_datos)
{
#define SERIAL_TIME 200
  static long t_serial_out=0;
  t_serial_out=millis();
  switch(p_serie)
  {
    case 0:
      while((Serial.available() < n_datos) && ((millis()-t_serial_out) < SERIAL_TIME));
      break;
    case 1:
      while((Serial1.available() < n_datos) && ((millis()-t_serial_out) < SERIAL_TIME));
      break;
    case 2:
      while((Serial2.available() < n_datos) && ((millis()-t_serial_out) < SERIAL_TIME));
      break;
    case 3:
      while((Serial3.available() < n_datos) && ((millis()-t_serial_out) < SERIAL_TIME));
      break;   
  }
  if((millis()-t_serial_out) < SERIAL_TIME)
    return 1;
  else
    return 0;  
}

void pruebas(void);

void pruebas(void)
{
  while(digitalRead(GO)!=0)
  {
    oled_texto("Calibra brujula",1,0,GRANDE,BLANCO);
    velocidad_robot = 15;  
  }
  espera_go();
  oled_borra_pantalla();
  
  oled_texto("Calibrando brujula...",1,0,GRANDE,BLANCO);
  Wire.beginTransmission(0X21);
  Wire.send("C");
  Wire.endTransmission();  
  gira_robot(velocidad_robot);
  delay(30000);
  para_robot();
  Wire.beginTransmission(0X21);
  Wire.send("E");
  Wire.endTransmission();
  oled_borra_pantalla();
  oled_texto("Calibracion terminada",1,0,GRANDE,BLANCO);
  delay(2000);
}
////////////////////////////////////////
// Archivo: delantero
//
////////////////////////////////////////

void juega_delantero(void);
void centra_delantero(void);
void manda_xbee(void);

void juega_delantero(void)
{
  rol_robot = (digitalRead(INT_JUGADOR));

  if(robot == ROBOT_NEXUS_9_2)
  {
#define CONSUMO_MAXIMO_ROLLER 30
  } 
  else
  {
#define CONSUMO_MAXIMO_ROLLER 30
  }   

  while(1)
  {
    //Actualizamos periodicamente todos los sensores y los motores
    actualiza_sensores();
    manda_xbee();

    centra_brujula(0);

    if(sensor_maximo>47)
    {
      centra_delantero();
      //direccion=48;
      activa_roller(0);
    }
    else
    {
      activa_roller(1);
      voy_detras_de_la_bola();

      //Salir de la esquina
      if(((us_izquierdo+us_derecho) < 45) && (us_trasero < 25))
      {
        direccion = 12;
      }
      if(((us_izquierdo+us_derecho) > 100) && (us_trasero < 25))
      {
        if((sensor_maximo > 24) && (sensor_maximo < 36))
          direccion=24;
        else if(sensor_maximo > 36)
          direccion=0; 
      }
      //Intentamos tirar a la porteria
      tira_porteria();

      if((distancia_bola > 6) || (direccion < 10) && (direccion > 14) && (consumo_roller < CONSUMO_MAXIMO_ROLLER))
      {
        velocidad_robot=80;
      }
      else
        velocidad_robot=100;
    }   

    actualiza_motores();
  }
}
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
int main(void)
{
	init();

	setup();
    
	for (;;)
		loop();
        
	return 0;
}

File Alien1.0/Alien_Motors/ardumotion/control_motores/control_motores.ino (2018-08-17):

#include <Wire.h>

#define LED 11  //Indicador de estado

//Pines potenciómetro
#define POT A4

//Pines del motor
#define PHASE 8      //rojo
#define ENABLE 9     //negro

//Pines del encoder
#define ENCODER1 2  //amarillo
#define ENCODER2 3  //blanco     

//variables para calcular la vel_real
long pos, tim;
volatile long encoderPos = 0;
long newposition = 0;
long oldposition = 0;
long tiempo = 0;          //Diferencia newtime-oldtime

unsigned long oldtime, newtime; //tiempos en poitivo

int vel_real, vel_real_pwm;            //Encoder
int error;               //V_consigna-V_real
int error_anterior = 0;  //Error en t-1
long integral = 0;        //Varable acumulativa para calcular la integral del error
int vel_proporcional;
int vel_integral;
int vel_derivativa;
int vel_error;           //vel_proporcional+vel_integral+vel_derivativa
int vel_motor;           //Velocidad de error ajustada pwm
long posicion;

//Constantes de control
int ConstanteProporcional = 1;
float ConstanteIntegral = 0.5;
float ConstanteDerivativa = 0.0005;

int rpm_max = 400;        //Velocidad máxima de los motores


int tipo = 0;             //0-->alante;1-->atras;2-->parar
long vel_consigna;        //Velocidad a la que queremos ir

void contar();
void avanzar (int v, int tipo);

void setup()
{
  pinMode(LED, OUTPUT);
  pinMode(PHASE, OUTPUT);
  pinMode(ENABLE, OUTPUT);
  pinMode(ENCODER1, INPUT_PULLUP);  //Sustituye a una resistencia(PULLUP)
  pinMode(ENCODER2, INPUT_PULLUP);  //Sustituye a una resistencia(PULLUP)

  Serial.begin(115200);

  attachInterrupt(digitalPinToInterrupt(ENCODER1), contar, RISING);

  //Iniciamos cronómetro
  oldtime = millis();

  digitalWrite(LED, HIGH);

}
void loop()
{
  //Constantemente medimos el tiempo
  newtime = millis();

  vel_consigna = map(analogRead(POT), 0, 1023, 0, rpm_max); //vel_consigna en rpm

  if (newtime - oldtime >= 100)
  {
    //Mide la velociad real
    tiempo = newtime - oldtime;
    oldtime = millis();         //Actualizamos el tiempo para hacer la diferecia del if
    newposition = encoderPos;   //Actualizamos la posicion
    posicion = newposition - oldposition;

    pos = (posicion * 60000);
    tim = long(tiempo * 245);   //12 pulsos=1rpm 20,4:1
    vel_real = pos / tim;       //Velocidad del encoder a rpm


    //Calculo del error
    error = vel_consigna - vel_real;

    //Control de velocidad proporcional
    vel_proporcional = ConstanteProporcional * error;

    //Control de velocidad integral
    integral += error * 0.1; //t(minutos)=0.0017
    vel_integral = integral * ConstanteIntegral;

    //Control de velocidad derivativo
    vel_derivativa = ((error - error_anterior) / 0.0017) * ConstanteDerivativa; //t(minutos)=0.0017
    error_anterior = error;

    //Control de velocidad PID
    vel_error = vel_proporcional + vel_integral + vel_derivativa;



    //Paso de rpm a pwm
    vel_motor = map(vel_error, 0, rpm_max, 0, 255); //Pasamos de rpm a pwm

    //Control de saturación
    if (vel_motor > 255)
      vel_motor = 255;
    if (vel_motor < 0)
      vel_motor = 0;

    avanzar(vel_motor, tipo);

    oldposition = newposition; // Actualizar la posicion para la siguiente entrada en el bucle
  }

  Serial.print("POT: ");
  Serial.print(vel_consigna);
  Serial.print("  \tREAL: ");
  Serial.print(vel_real);
  Serial.print("  \tPWM: ");
  Serial.print(vel_real_pwm);
  Serial.print("  \tMOTOR: ");
  Serial.print(vel_motor);
  Serial.print("\tERROR: ");
  Serial.println(error);

}

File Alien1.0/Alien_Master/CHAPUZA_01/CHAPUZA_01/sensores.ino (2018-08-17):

void actualiza_lectura_bola(void)
{
  byte bola = 255;

  Serial2.write('t');
  while (Serial2.available() < 3);
  bola = Serial2.read();
  distancia_bola = Serial2.read();
  bola_cerca = Serial2.read();

  if (bola != 255)
  {
    if (bola % 2 != 0)
      bola++;
    bola_actual = (bola / 2);
  }
  else
    bola_actual = bola;

  Serial2.write('b');
  while (Serial2.available() < 1);
  bola_cerca = Serial2.read();
}

void actualiza_lectura_us(void)
{
  Serial3.write('m');
  while (Serial3.available() < NUMERO_US);
  for (int x = 0; x < NUMERO_US; x++)
  {
    medidas_us [x] = Serial3.read();
  }
}



void actualiza_lectura_brujula(void)
{
  int pwm = 0;
  for (int x = 0; x < 4; x++)
    pwm += pulseIn(PWM_BRUJULA, HIGH);

  angulo_brujula = (pwm / 4);
  angulo_brujula_abs = abs(angulo_brujula);
}

void centrar_p ()
{
  error_lateral = (medidas_us[0] - medidas_us[2]);
  error_lateral_abs = abs(error_lateral);

  if ((error_lateral_abs > 30))
    ajuste = 15;
  else
    ajuste = 0;

  error_trasero = (CENTRADO_TRASERO_P + ajuste) - medidas_us[1];
  error_trasero_abs = abs(error_trasero);


  if (angulo_brujula_abs < MARGEN_BRUJULA)
  {
    if (caso_suelo == 3)
    {
      Serial1.write('v');
      Serial1.write (velocidad_actual);
      if (medidas_us[0] > medidas_us[2])
        Serial1.write('B');
      else
        Serial1.write('P');
    }
    else if ((error_trasero_abs > MARGEN_TRASERO))
    {
      integral_t += error_trasero;
      integral_t = constrain(integral_t, -MARGEN_I, MARGEN_I);

      if (error_trasero_abs < (MARGEN_TRASERO + 1))
        integral_t = 0;

      velocidad_actual = (((error_trasero_abs + ((integral_t * KI) / 1000.0)) * KP) / 100.0);
      velocidad_actual  = constrain(velocidad_actual, VELOCIDAD_MINIMA, velocidad_maxima);

      Serial1.write('v');
      Serial1.write (velocidad_actual);
      if (error_trasero > 0)
      {
        if (medidas_us[0] > (medidas_us[2] + 30))
          Serial1.write('C');
        else if (medidas_us[0] > (medidas_us[2] + 15))
          Serial1.write('B');
        else if (medidas_us[2] > (medidas_us[0] + 30))
          Serial1.write('O');
        else if (medidas_us[2] > (medidas_us[0] + 15))
          Serial1.write('P');
        else
          Serial1.write('A');
      }
      else
      {
        if (medidas_us[0] > (medidas_us[2] + 30))
          Serial1.write('K');
        else if (medidas_us[0] > (medidas_us[2] + 15))
          Serial1.write('J');
        else if (medidas_us[2] > (medidas_us[0] + 40))
          Serial1.write('G');
        else if (medidas_us[2] > (medidas_us[0] + 15))
          Serial1.write('H');
        Serial1.write('I');
      }
    }
    else if ((error_lateral_abs > MARGEN_LATERAL ) && ((medidas_us[0] + medidas_us[2]) > 145))
    {
      integral_l += error_lateral;
      integral_l = constrain(integral_l, -MARGEN_I, MARGEN_I);

      if (error_lateral_abs < (MARGEN_LATERAL + 1))
        integral_l = 0;

      velocidad_actual = (((error_lateral_abs + ((integral_l * KI) / 1000.0)) * KP) / 100.0);
      velocidad_actual  = constrain(velocidad_actual, VELOCIDAD_MINIMA, velocidad_maxima);

      Serial1.write('v');
      Serial1.write (velocidad_actual);
      if (error_lateral > 0)
        Serial1.write('E');
      else
        Serial1.write('M');
    }
    else
    {
      Serial1.write('v');
      Serial1.write (velocidad_maxima);
      Serial1.write('x');
    }
  }
  else
  {
    Serial1.write('v');
    Serial1.write (velocidad_maxima);
    Serial1.write('x');
  }
}

void centrar_d ()
{
  error_lateral = (medidas_us[0] - medidas_us[2]);
  error_lateral_abs = abs(error_lateral);

  if ((error_lateral_abs > 30))
    ajuste = 15;
  else
    ajuste = 0;

  error_trasero = (CENTRADO_TRASERO_D + ajuste) - medidas_us[1];
  error_trasero_abs = abs(error_trasero);


  if (angulo_brujula_abs < MARGEN_BRUJULA)
  {
    if (caso_suelo == 3)
    {
      Serial1.write('v');
      Serial1.write (velocidad_actual);
      if (medidas_us[0] > medidas_us[2])
        Serial1.write('B');
      else
        Serial1.write('P');
    }
    else if ((error_trasero_abs > MARGEN_TRASERO))
    {
      integral_t += error_trasero;
      integral_t = constrain(integral_t, -MARGEN_I, MARGEN_I);

      if (error_trasero_abs < (MARGEN_TRASERO + 1))
        integral_t = 0;

      velocidad_actual = (((error_trasero_abs + ((integral_t * KI) / 1000.0)) * KP) / 100.0);
      velocidad_actual  = constrain(velocidad_actual, VELOCIDAD_MINIMA, velocidad_maxima);

      Serial1.write('v');
      Serial1.write (velocidad_actual);
      if (error_trasero > 0)
      {
        if (medidas_us[0] > (medidas_us[2] + 30))
          Serial1.write('C');
        else if (medidas_us[0] > (medidas_us[2] + 15))
          Serial1.write('B');
        else if (medidas_us[2] > (medidas_us[0] + 30))
          Serial1.write('O');
        else if (medidas_us[2] > (medidas_us[0] + 15))
          Serial1.write('P');
        else
          Serial1.write('A');
      }
      else
      {
        if (medidas_us[0] > (medidas_us[2] + 30))
          Serial1.write('K');
        else if (medidas_us[0] > (medidas_us[2] + 15))
          Serial1.write('J');
        else if (medidas_us[2] > (medidas_us[0] + 40))
          Serial1.write('G');
        else if (medidas_us[2] > (medidas_us[0] + 15))
          Serial1.write('H');
        Serial1.write('I');
      }
    }
    else if ((error_lateral_abs > MARGEN_LATERAL ) && ((medidas_us[0] + medidas_us[2]) > 145))
    {
      integral_l += error_lateral;
      integral_l = constrain(integral_l, -MARGEN_I, MARGEN_I);

      if (error_lateral_abs < (MARGEN_LATERAL + 1))
        integral_l = 0;

      velocidad_actual = (((error_lateral_abs + ((integral_l * KI) / 1000.0)) * KP) / 100.0);
      velocidad_actual  = constrain(velocidad_actual, VELOCIDAD_MINIMA, velocidad_maxima);

      Serial1.write('v');
      Serial1.write (velocidad_actual);
      if (error_lateral > 0)
        Serial1.write('E');
      else
        Serial1.write('M');
    }
    else
    {
      Serial1.write('v');
      Serial1.write (velocidad_maxima);
      Serial1.write('x');
    }
  }
  else
  {
    Serial1.write('v');
    Serial1.write (velocidad_maxima);
    Serial1.write('x');
  }
}

void chuta(void)
{
  if (crono_chutador < (millis() - 800))
  {
    digitalWrite(CAL_BRUJULA, HIGH);
    delay(1);
    digitalWrite(CHUTADOR, HIGH); 
    crono_chutador = millis();
  }
}

void suelo1 (void)
{
  /*switch (caso_suelo)
  {
    case 0:
      caso_suelo = 1;
      break;
    case 2:
      caso_suelo = 5;
      break;
    case 4:
      caso_suelo = 8;
      break;
  }*/
  caso_suelo = 1;
  contador_salida = 2;
}

void suelo2 (void)
{
  /*switch (caso_suelo)
  {
    case 0:
      caso_suelo = 2;
      break;
    case 1:
      caso_suelo = 5;
      break;
    case 3:
      caso_suelo = 6;
      break;
  }*/
  caso_suelo = 2;
  contador_salida = 2;
}
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
